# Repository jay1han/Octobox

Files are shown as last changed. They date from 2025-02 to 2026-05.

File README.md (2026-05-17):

# Octobox

Box for OrangePi Zero 2W running Fluidd/Moonraker/Klipper

# Hardware

## Components

### Actuator TB6612

Controls the actuator that opens/closes door.

[Instructables](https://www.instructables.com/Driving-Small-Motors-With-the-TB6612FNG/)

### Temperature sensor MLX90614

Reads the bed temperature via I2C.

[Instructables](https://www.instructables.com/MLX90614-Non-Contact-Infrared-Temperature-Sensor-W/)

### Relays

4-channel 5V module from [AliExpress](https://fr.aliexpress.com/item/1005007538301230.html).
Usage:
[Instructables](https://www.instructables.com/5V-4-Channel-Relay-Module-With-Arduino/)

- Box fan (12V): 120mm fan at the rear of the cabinet
- Bed cooler (12V): 80mm fan cools the bed after a print
- Printer power (220V)

### 2N7000 Transistor

Pack from [AliExpress](https://fr.aliexpress.com/item/1005006203763174.html).
Usage:
[2N7000 as switch](https://electronzap.com/brief-n-channel-enhancement-mode-mosfet-switch-circuit-2n7000-transistor/)

- Camera light (5V)
- CPU fan (5V): small 40mm fan cooling the CPU

## OrangePi Zero 2W pinout

| Number | GPIO | Alt | Value | | Number | GPIO | Alt | Value |
|---|---|---|---|---|---|---|---|---|
| | 3.3V | | I2C VCC | | | 5V | | |
| 264 | PI8  | SDA.1 | I2C SDA | | | 5V | | Power 5V |
| 263 | PI7  | SCL.1 | I2C SCL | | | GND  | | Power GND  |
| 269 | PI13 | PWM3 TXD.4  | | | 224 | PH0  | TXD.0 | |
| | GND  | | I2C GND | | 225 | PH1  | RXD.0 | |
| 226 | PH2  | TXD.5 | | | 257 | PI01 | | |
| 227 | PH3  | RXD.5 | | | | GND  | | |
| 261 | PI5  | SCL.0 TXD.2 | | | 270 | PI14 | PWM4 RXD.4  | Pusher PWM |
| | 3.3V | | Pusher VCC | | 228 | PH04 | | |
| 231 | PH7  | MOSI.1 | | | | GND  | | Pusher GND |
| 232 | PH8  | MISO.1 | | | 262 | PI6  | SDA.0 RXD.2 | Pusher 2 |
| 230 | PH6  | SCLK.1 | | | 229 | PH5  | CE.0 | Pusher 1 |
| | GND  | | | | 233 | PH9  | CE.1 | |
| 266 | PI10 | SDA.2 RXD.3 | | | 265 | PI9  | SCL.2 TXD.2 | Light |
| 256 | PI00 | Flash | | | | GND  | | MOSFET GND |
| 271 | PI15 | | | | 267 | PI11 | PWM1 | Fan40 |
| 268 | PI12 | PWM2 | | | | GND  | | Relay GND  |
| 258 | PI02 | | | | 76 | PC12 | | Fan120 |
| 272 | PI16 | | | | 260 | PI04 | | Printer |
| | GND  | | | | 259 | PI03 | | Fan80 |
	
# Software 

The software is a daemon started from systemd.
It listens on port `8080` and provides a basic HTTP server,
with a simple HTML page showing its current state.
The page contains minimal Javascript to update itself when needed.

The daemon also listens on port `8088` to serve [Moonraker's commands](#moonraker-interface).

## States

| State | When | Look for | Change to | Also do |
|---|---|---|---|---|
| (Initial) | booting | | OFF | retract Pusher, switch everything OFF |
| OFF | printer is off | event `power` | ON | switch Relay ON |
| ON | printer is powering on | Moonraker is ready | IDLE | |
| IDLE | ready for print | event `power` | OFF | switch everything OFF |
| | | Moonraker is printing | PRINTING  | switch Fan ON, Flash ON |
| PRINTING  | print job running | Moonraker is stopped  | COOLING | switch off Printer, start Cooler, extend Pusher |
| | | event `cancel` | PRINTING  | cancel job |
| COOLING | print job ended | bed temp < 35C | OFF | retract Pusher, switch everything OFF |
| | | event `power` | OFF | retract Pusher, switch everything OFF |
| (Any) | | event `reboot` | N/A | switch everything OFF then reboot |

## Moonraker API

Moonraker's
[HTTP API](https://moonraker.readthedocs.io/en/latest/external_api/introduction/#http-api-overview)
are used to update the daemon's internal state.

## Moonraker interface

The daemon provides an endpoint for Moonraker's
[HTTP devices](https://moonraker.readthedocs.io/en/latest/configuration/#generic-http-devices)
interface.

Moonraker must be configured

# Documents

- `Orange.pptx` shows the cabling of the Opi Zero 2W.
- `.FCStd` files for 3D models.
    - `CapL` : the filament guide at the top of the Z pole
    - `Fan8` : casing for the cooling fan
    - `KPS-CameraHD 2w` : the camera bracket
    - `Octobox 2W simple` : frame for the Opi and the board
    - `Wirecover` : to isolate the terminals of the power supply
    - `Touch` : housing for the touch sensor (ambient light)
    - `horiz2` : horizontal feeder for filament spool

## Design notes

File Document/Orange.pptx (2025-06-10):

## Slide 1

actual

Relay

1K

1K

1K

CPU

Cooler

10K

10K

Box

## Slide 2

enhanced

USB GND

1K

10K

1K

CPU Fan

1K

Relay

1K

Fan80

10K

10K

Fan120

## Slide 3

For USB

USB GND

1K

10K

1K

100

CPU Fan

1K

Relay

1K

Fan80

10K

10K

Fan120

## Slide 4

5V
GND
Fan80
Fan120
Relay
CPU Fan
Flash

5V:
- Flash
- Relay
- Pusher (?)
- CPU fan
- (Light)
12V:
- Fan120
- Fan80
64x44 M2
Direct:
- I2C(4)
- Touch in(3)

Flash

2K

PWM
A2
A1
En/

CPU Fan

Relay

2K

Fan120

Fan80

GND
3V3

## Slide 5

5V
GND
Fan80
Fan120
Relay
CPU Fan
Flash

5V:
- Flash
- Relay
- CPU fan
12V:
- Fan120
- Fan80
64x44 M2
Gate pull-down 10K
Flyback 1N4001 (50V)
Solid power 24AWG
Striped single 26AWG
Dotted signal 30AWG

10K

10K

Flash

CPU Fan

Relay

Fan120

Fan80

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
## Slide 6

5V:
- Flash
- Relay
- CPU fan
12V:
- Fan120
- Fan80
64x44 M2
Gate pull-down 47K
Flyback 1N4001 (50V)
Solid power 24AWG
Striped single 26AWG
Dotted signal 30AWG

10K

10K

Fan120

Fan80

10K

Flash

CPU Fan

Relay

10K

10K

PWM
A2
A1
En/

3V3

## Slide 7

5V:
- Flash
- Relay
- CPU fan
12V:
- Fan120
- Fan80
64x44 M2
Gate pull-down 47K
Flyback 1N4001 (50V)
Solid power 24AWG
Striped single 26AWG
Dotted signal 30AWG

10K

10K

Fan120

Fan80

10K

PWM
A2
A1
En/

3V3

Flash

CPU Fan

Relay

10K

10K

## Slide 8

5V:
- Flash
- Relay
- Pusher (?)
- (Light)
12V:
- Fan120
- Fan80
64x44 M2
Direct:
- I2C(4)
- Touch in(3)

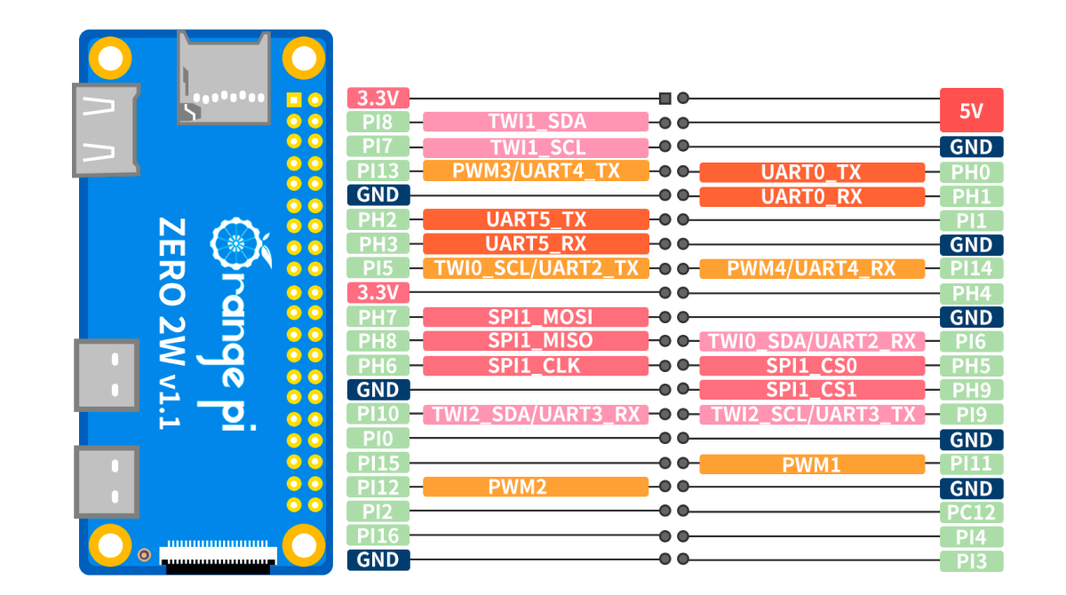
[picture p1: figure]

Pusher VCC

PWR 5V
PWR GND

I2C SCL
I2C VCC

I2C GND
I2C SDA
Pusher EN/
Pusher 1
Pusher 2

Pusher PWM
Flash
Relay
Fan80

CPU Fan
Fan120

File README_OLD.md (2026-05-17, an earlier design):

# Octobox OLD

Box for OrangePi Zero 2W running Octoprint for KP3S

## Server

You need to obtain an API key from Octoprint and store it in `api.key` in plain text.

### States

Modified for remote temperature sensor.

| State | When | Look for | Change to | Also do |
|---|---|---|---|---|
| (Initial) | starting Octobox | | Off | retract Pusher, capture Camera, switch everything OFF |
| Off | printer is off | event `power` | On | switch Relay ON, start Camera, start timeout |
| | | event `reboot` | N/A | reboot |
| | | event `refresh` | | capture image |
| On | printer is powering on | Octo is `Operational`  | Idle | |
| | | Octo has error | Off | switch everything OFF |
| | | Timeout elapsed | Off | switch everything OFF |
| | | event `refresh` | | capture image |
| Idle | ready for print | event `power` | Off | switch everything OFF |
| | | event `reboot` | N/A | reboot |
| | | Octo has error | Off | switch everything OFF |
| | | Octo is `Printing` | Printing  | |
| | | event `refresh` | | restart video |
| Printing  | print job running | Octo has error | Cooling | switch off Printer, start Cooler, extend Pusher |
| | | Octo is not `Printing` | Cooling | switch off Printer, start Cooler, extend Pusher |
| | | event `cancel` | Cooling | cancel Octo job, switch off Printer, start Cooler and Pusher |
| Cooling | print job ended | Octo has error | Off | retract Pusher, switch everything OFF |
| | | bed temp < 35C | Off | retract Pusher, switch everything OFF |
| | | event `power` | Off | retract Pusher, switch everything OFF |

## Peripherals

All methods take an optional argument to set the value,
or return the current value if no argument is given.
This module requires the module `python3-periphery`
and to be given access. See `install.sh`.

- `flash()` to switch the LED illuminating the camera.
This is used exclusively by the Camera module

- `fan()` to switch the cooling fan.

- `relay()` to switch the printer.

### Sensor

The MLX90614 allows monitoring ambient and bed temperatures at all times.
CPU sensor is now in this module.

### Camera

Upon initialization, kills current ustreamer if one is running.
When active, ustreamer is available at the URL
`http://localhost:8080`.

- `start()` starts ustreamer.

- `stop()` stops it. Calls `capture()`.

- `capture()` captures a still image into `/var/www/html/image.jpg`.

### Pusher

The motor is controlled by a TB6612FNG module.

## Display

This actually just updates the data files that are used by the HTML to display the page.

- `localIP` contains the local IP address.

- `state` contains the title of the document, which is the state returned by Octoprint.

- `temps` contains HTML snippet showing temperatures.

- `jobInfo` contains HTML snippet showing Job information (if any).

## Octoprint

This uses Octoprint's REST API to interact with it.
You need to obtain an API key from Octoprint and store it in `api.key` in plain text.

- Queries : `job` or `printer` queries.

- Requests : `connection` request to connect or disconnect the printer.

## Socket library

The file `/usr/share/octobox/socket` is used to pass events.
A user must first `lock()` it, then `read()` to or `write()` from it, 
then `free()` it.

## CGI

The GPI module uses the Socket library to send events to the running Octobox process.

- `power` to switch the printer.

- `reboot` to reboot Octobox.

- `cancel` cancels the print.

- `refresh` captures a new image.

## Documents

- `Orange.pptx` shows the cabling of the Opi Zero 2W.

- `.FCStd` files for 3D models.

    - `CapL` : the filament guide at the top of the Z pole
    
    - `Fan8` : casing for the cooling fan
    
    - `KPS-CameraHD 2w` : the camera bracket
    
    - `Octobox 2W simple` : frame for the Opi and the board
    
    - `Wirecover` : to isolate the terminals of the power supply
    
    - `Touch` : housing for the touch sensor (ambient light)

    - `horiz2` : horizontal feeder for filament spool
	
### OrangePi pinout

| Number | GPIO | Alt | Value | Color  |
|---|---|---|---|---|
| | 3.3V | | Pusher VCC | Orange |
| 264 | PI8  | SDA.1 | | |
| 263 | PI7  | SCL.1 | | |
| 269 | PI13 | PWM3 TXD.4  | Pusher PWM | Green  |
| | GND  | | Pusher GND | Black  |
| 226 | PH2  | TXD.5 | | |
| 227 | PH3  | RXD.5 | | |
| 261 | PI5  | SCL.0 TXD.2 | I2C SCL | Yellow |
| | 3.3V | | I2C VCC | Orange |
| 231 | PH7  | MOSI.1 | | |
| 232 | PH8  | MISO.1 | | |
| 230 | PH6  | SCLK.1 | | |
| | GND  | | | |
| 266 | PI10 | SDA.2 RXD.3 | | |
| 256 | PI00 | | Pusher EN  | Maroon |
| 271 | PI15 | | | |
| 268 | PI12 | PWM2 | CPU Fan | Green  |
| 258 | PI02 | | | |
| 272 | PI16 | | | |
| | GND  | | | |

| Number | GPIO | Alt | Value | |
|---|---|---|---|---|
| | 5V | | | |
| | 5V | | Power 5V  | Red |
| | GND  | | Power GND | Black  |
| 224 | PH0  | TXD.0 | | |
| 225 | PH1  | RXD.0 | | |
| 257 | PI01 | | | |
| | GND  | | | |
| 270 | PI14 | PWM4 RXD.4  | | |
| 228 | PH04 | | | |
| | GND  | | I2C GND | Violet |
| 262 | PI6  | SDA.0 RXD.2 | I2C SDA | Cream  |
| 229 | PH5  | CE.0 | | |
| 233 | PH9  | CE.1 | Pusher 1  | Blue |
| 265 | PI9  | SCL.2 TXD.2 | Pusher 2  | Violet |
| | GND  | | | |
| 267 | PI11 | PWM1 | Flash | Grey |
| | GND  | | | |
| 76 | PC12 | | Relay | Cream  |
| 260 | PI04 | | Fan120 | Blue |
| 259 | PI03 | | Fan80 | Violet |

## TODO

### Hardware

- Actuator

- Temperature sensor(s): MLX90614

	- Turn off printer at job's end and turn on cooling fan
	
	- Use sensor to monitor bed temperature and turn off cooling fan
	
- Recheck install script

- Better lighting for camera

### Software

HTTP GETtable file `http://octo2w.local/info` returns the following information
in INI format (`key=value`):

| Field | Type | Example |
|---|---|---|
| filename | string | `octobox-part` |
| completion  | float  | `15.6` |
| remaining | HH:MM  | `01:32` |

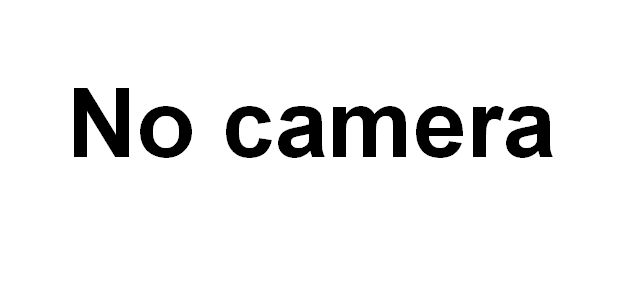
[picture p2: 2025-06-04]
Server/files/nocamera.jpg

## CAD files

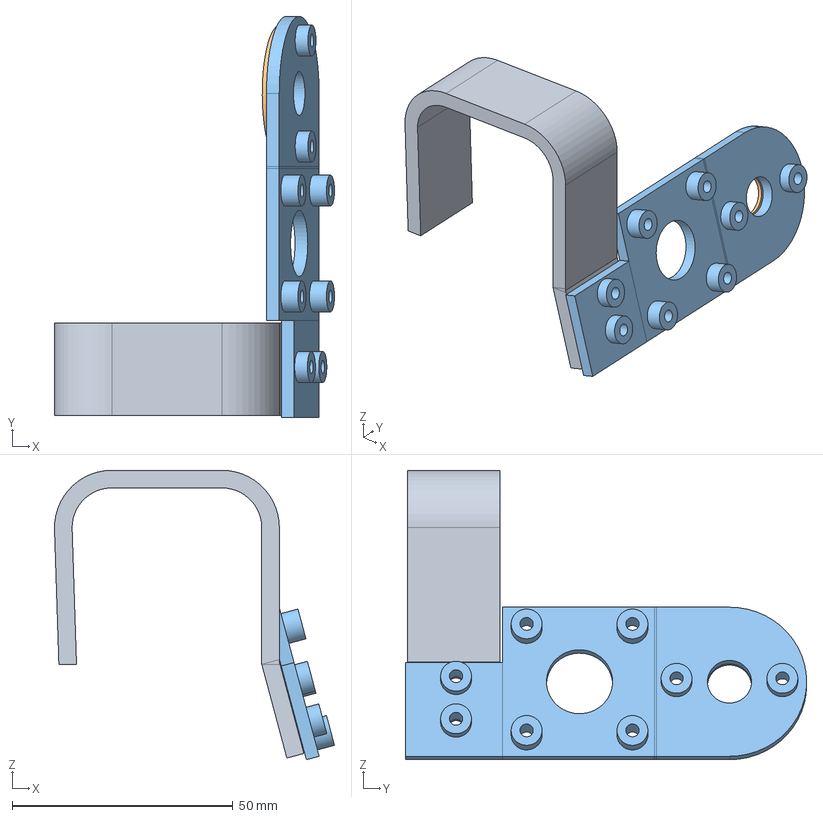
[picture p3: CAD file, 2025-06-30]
Design/KPS-CameraHD bigled.FCStd
63.5 x 91.0 x 65.6 mm
Clip
Bigled
Camholes

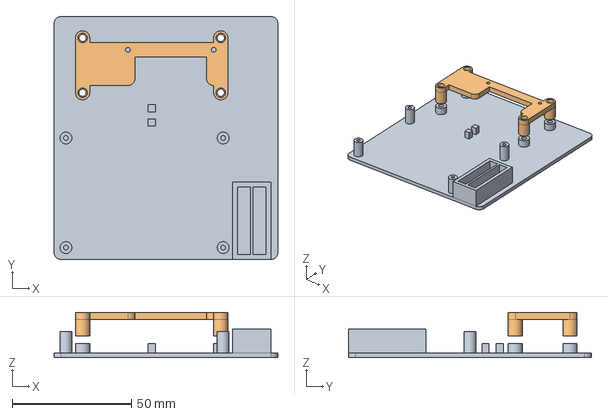
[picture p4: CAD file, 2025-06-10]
Document/Octobox 2W relays.FCStd
94.0 x 102.0 x 19.0 mm
Base
Fan

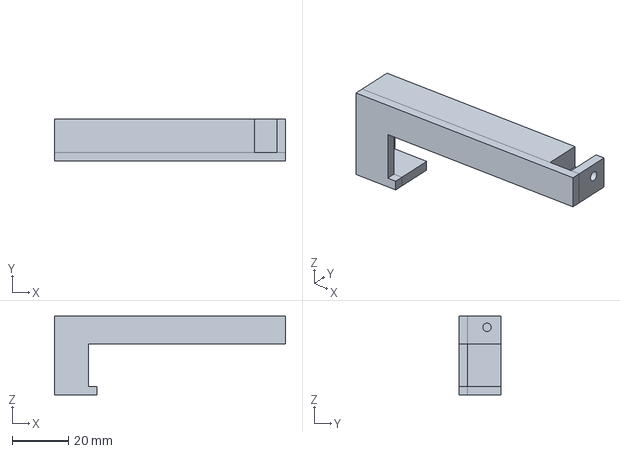
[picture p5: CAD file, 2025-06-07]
Design/Wirecover.FCStd
82.0 x 15.0 x 28.0 mm

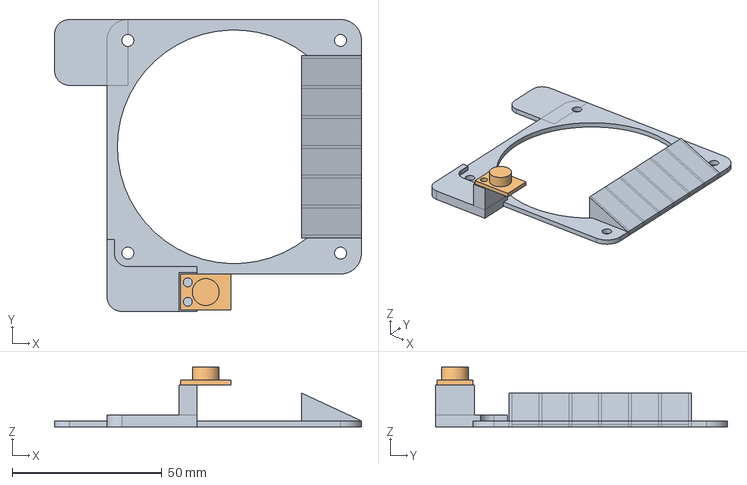
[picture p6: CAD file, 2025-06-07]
Document/Fan8-slant.FCStd
102.5 x 97.5 x 20.0 mm
Vent
Sensor

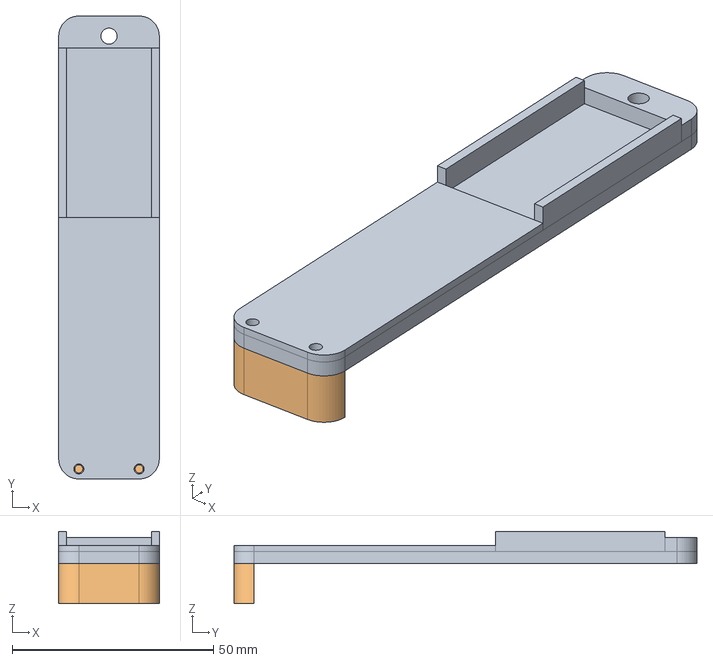
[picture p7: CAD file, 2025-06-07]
Design/Pusher.FCStd
25.0 x 115.0 x 18.0 mm
Tab

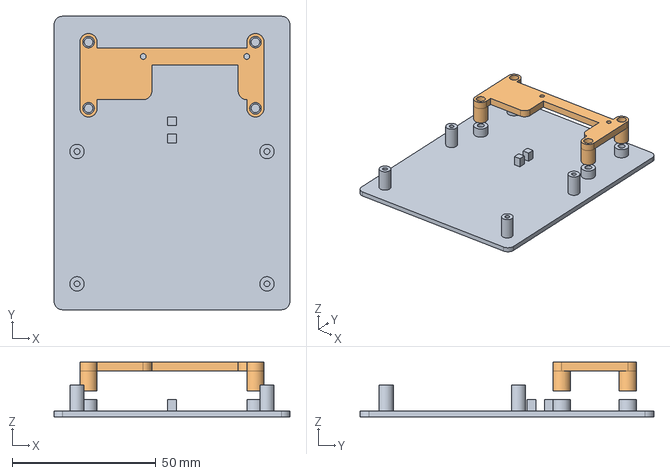
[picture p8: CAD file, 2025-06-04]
Document/Octobox 2W double.FCStd
82.0 x 102.0 x 19.0 mm
Base
Fan

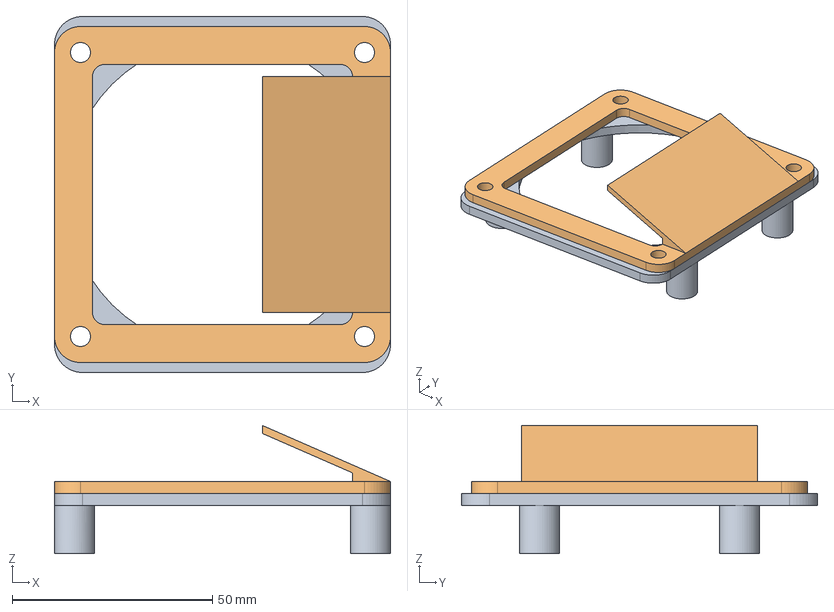
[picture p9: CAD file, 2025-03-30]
Design/Fan8.FCStd
84.0 x 89.0 x 32.0 mm
Vent

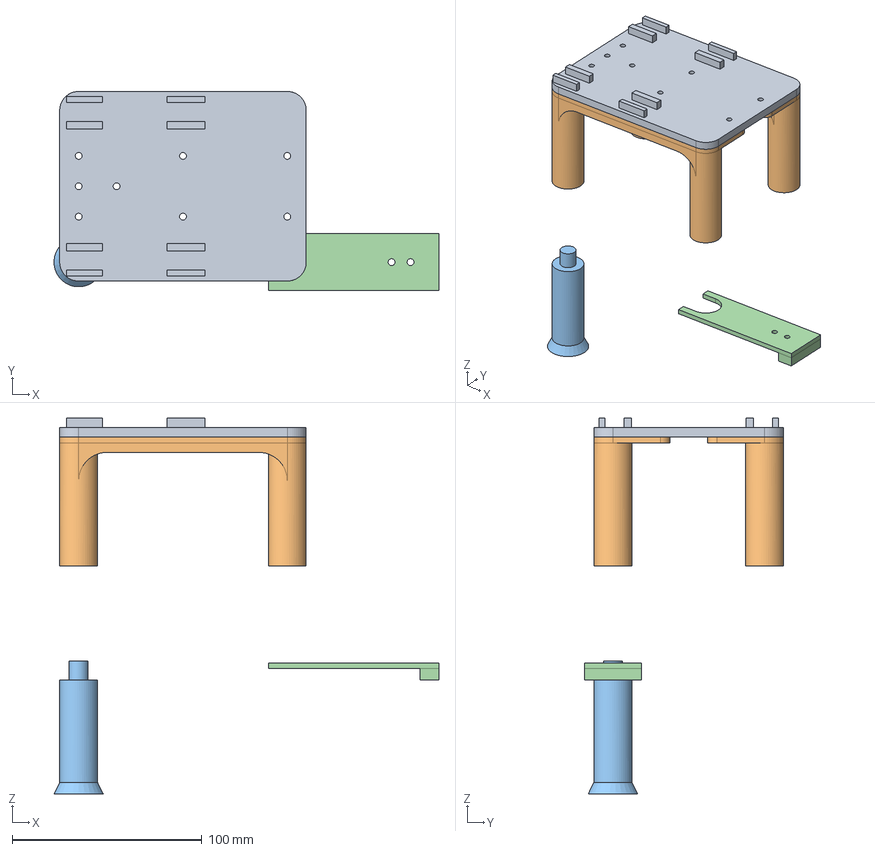
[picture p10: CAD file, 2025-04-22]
Document/Support_long.FCStd
203.0 x 105.0 x 198.0 mm
Top
Mid1 x 2
Leg1
Pusher

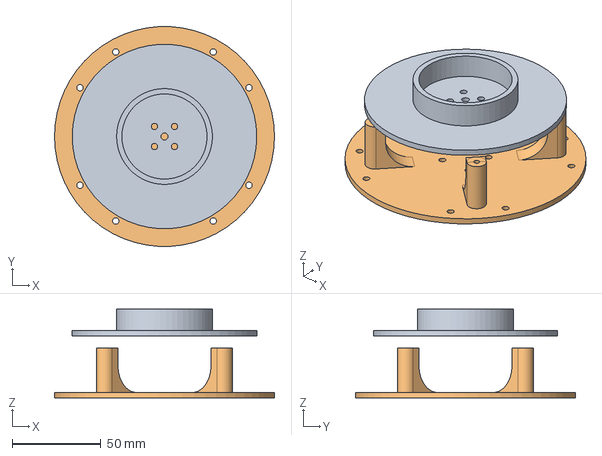
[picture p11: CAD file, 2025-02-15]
Design/horiz2.FCStd
124.0 x 123.8 x 50.0 mm
Wheel
Mid

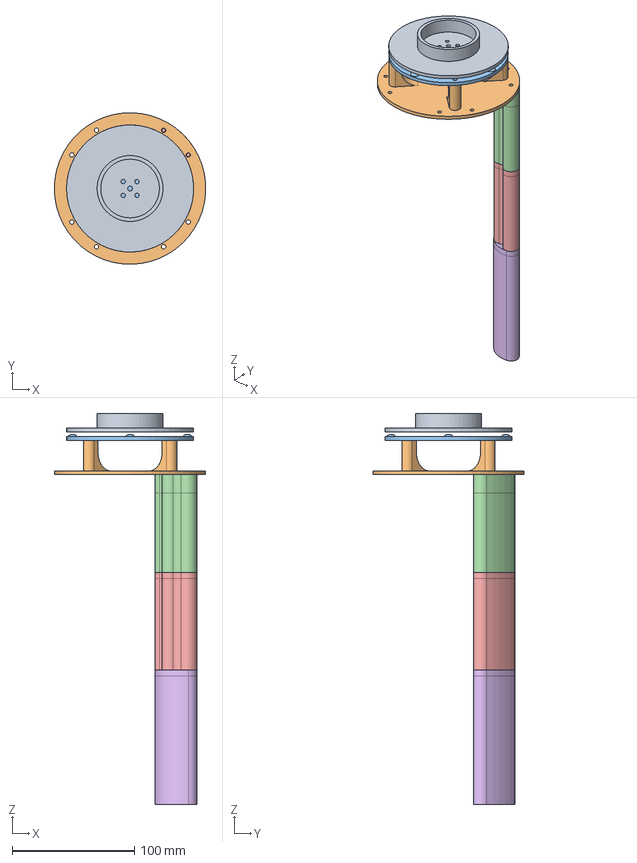
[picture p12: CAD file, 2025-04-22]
Document/horiz2.FCStd
123.9 x 123.9 x 320.0 mm
Wheel
Mid
Top
Leg1
Foot1
Shoe1

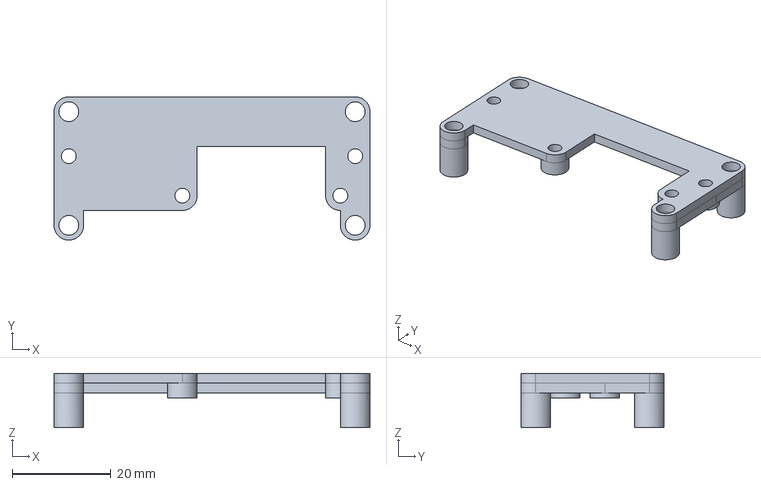
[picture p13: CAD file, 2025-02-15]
Design/Octobox 2W simple.FCStd
64.0 x 29.0 x 11.0 mm

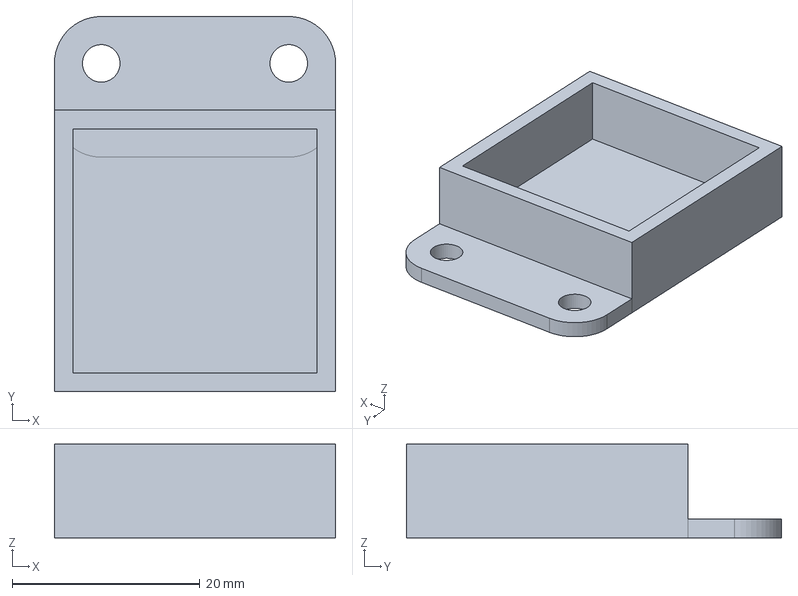
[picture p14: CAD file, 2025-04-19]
Document/Touch.FCStd
30.0 x 40.0 x 10.0 mm

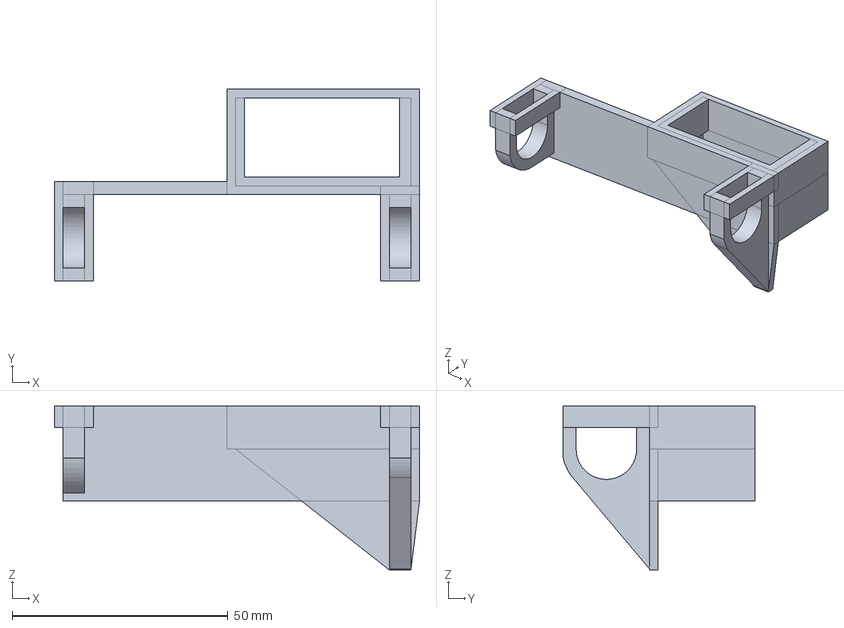
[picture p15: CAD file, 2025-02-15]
Design/CapL.FCStd
84.6 x 44.4 x 38.0 mm

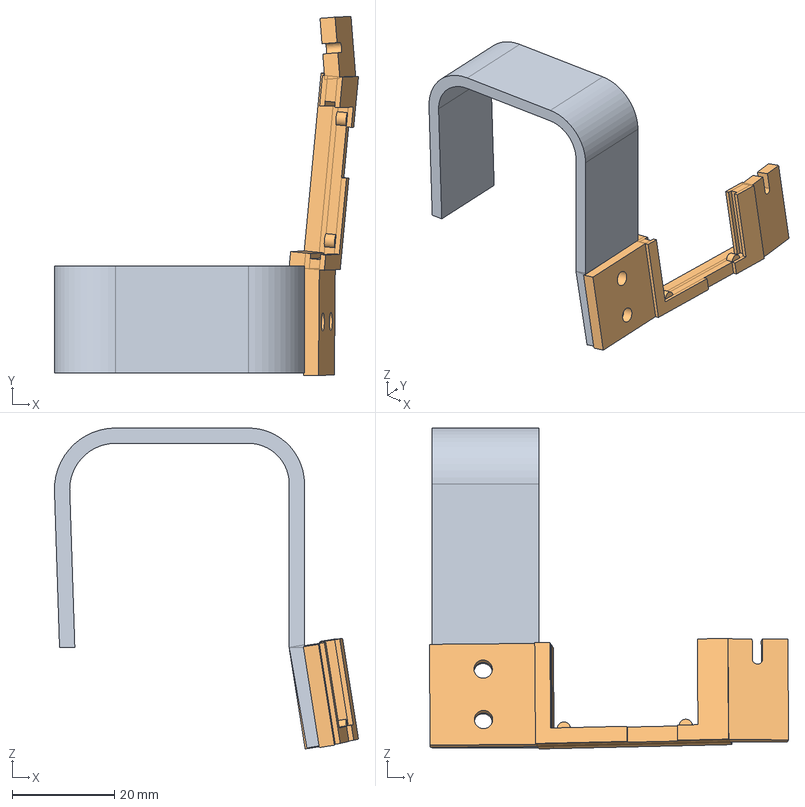
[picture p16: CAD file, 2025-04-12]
Document/KPS-CameraHD 2w.FCStd
59.6 x 70.4 x 62.9 mm
Clip
Frame

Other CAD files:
Design/CapGuide.FCStd
Document/Fan8.FCStd
Design/horiz.FCStd
Document/Octobox 2W simple.FCStd
Design/Cap.FCStd
Design/Cap_straight_slot.FCStd
Design/KPS-CameraHD 2w.FCStd
Design/Support_long.FCStd
Design/Touch.FCStd

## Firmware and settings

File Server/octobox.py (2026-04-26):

#!/usr/bin/python3

from time import sleep
from datetime import datetime, timedelta
from enum import Enum
import sys, subprocess

from octo_periph import Peripheral, Camera
from octo_disp import Display
from octo_print import Octoprint
from octo_socket import Socket

tempCold = 35.0

class State(Enum):
    Off      = 0
    On       = 1
    Idle     = 2
    Printing = 3
    Cooling  = 4

class Octobox:
    def __init__(self):
        self.state = State.Off
        self.octo_state = ''
        self.timeout = None
        self.elapsed = 0

        self.p = Peripheral()
        self.c = Camera(self.p)
        self.o = Octoprint()
        self.d = Display()
        self.s = Socket()

        self.d.setState('Printer Off')

    def __del__(self):
        pass

    def setTimeout(self, seconds):
        if seconds == 0:
            self.timeout = None
        else:
            self.timeout = datetime.now() + timedelta(seconds = seconds)

    def isTimedout(self):
        if self.timeout is not None and datetime.now() > self.timeout:
            self.timeout = None
            print('Timeout', file=sys.stderr)
            return True
        else:
            return False

    def powerOff(self):
        print('Power Off', file=sys.stderr)
        self.c.stop()
        self.p.fan(False)
        self.p.cooler(False)
        self.p.pusher(False)
        self.p.power(False)
        self.p.cpu(False)

    def powerOn(self):
        print('Power On', file=sys.stderr)
        self.d.clearInfo()
        self.p.power(True)
        self.p.fan(True)
        self.p.cpu(True)

    def reboot(self):
        print('Reboot', file=sys.stderr)
        self.powerOff()
        self.p.stop()
        ps = subprocess.run(['/usr/sbin/systemctl', 'reboot'])
        sys.exit(0)
    
    def loop(self):
        octo_state = self.o.getState()
        event = self.s.read()
        tempExt, tempBed = self.o.getTemp()
        tempCpu, tempOut, tempAmb = self.p.temps()

        if event != '' or self.octo_state != octo_state:
            print(f'State {self.state}: State "{octo_state}", Event "{event}"', file=sys.stderr)
            self.octo_state = octo_state

        if self.state == State.Off:
            if octo_state.startswith('Operational'):
                self.setTimeout(0)
                self.state = State.Idle
            elif event == 'refresh':
                self.c.capture()
            elif event == 'power':
                self.powerOn()
                self.c.start()
                sleep(1)
                self.o.connect()
                self.setTimeout(15)
                self.state = State.On
            elif event == 'reboot':
                self.reboot()

        elif self.state == State.On:
            if event == 'refresh':
                self.c.capture()
            elif octo_state.startswith('Operational'):
                self.setTimeout(0)
                self.state = State.Idle
            elif octo_state.startswith('Error') or octo_state.startswith('Offline'):
                print('Error', file=sys.stderr)
                self.o.disconnect()
                self.powerOff()
                self.state = State.Off
            elif self.isTimedout():
                self.o.disconnect()
                self.powerOff()
                self.state = State.Off

        elif self.state == State.Idle:
            if octo_state.startswith('Printing'):
                print('Print start', file=sys.stderr)
                self.state = State.Printing
                self.d.start()
            elif octo_state.startswith('Error') or octo_state.startswith('Offline'):
                print('Error', file=sys.stderr)
                self.o.disconnect()
                self.powerOff()
                self.state = State.Off
            elif event == 'refresh':
                self.c.refresh()
            elif event == 'power':
                print('Power Off', file=sys.stderr)
                self.o.disconnect()
                self.powerOff()
                self.state = State.Off
            elif event == 'reboot':
                self.reboot()

        elif self.state == State.Printing:
            if not octo_state.startswith('Printing'):
                self.state = State.Cooling
            elif event == 'refresh':
                self.c.refresh()
            elif event == 'cancel':
                self.o.cancel()
                self.state = State.Cooling
                
            if self.state == State.Cooling:
                print('Print ended', file=sys.stderr)
                self.d.end()
                self.p.cooler(True)
                self.p.pusher(True)

        elif self.state == State.Cooling:
            if octo_state.startswith('Error'):
                print('Error', file=sys.stderr)
            if tempOut < tempCold or tempOut < (tempAmb + 3.0):
                print('Cold', file=sys.stderr)
                self.state = State.Off
            elif event == 'power':
                print('Power Off', file=sys.stderr)
                self.state = State.Off
            elif event == 'refresh':
                self.c.refresh()
                
            if self.state == State.Off:
                self.o.disconnect()
                self.powerOff()
                
        self.d.setTemps(tempAmb, tempExt, tempBed, tempOut, tempCpu,
                        tempCold if self.state == State.Cooling else 0.0)
        
        if self.state == State.Off:
            self.d.setState('Printer Off')
        elif self.state == State.Idle:
            self.d.setState(octo_state)
            jobInfo = self.o.getJobInfo()
            self.d.setJobInfo(jobInfo)
        elif self.state == State.Printing:
            self.d.setState(octo_state)
            jobInfo = self.o.getJobInfo()
            self.elapsed = jobInfo.currentTime
            self.d.setJobInfo(jobInfo)
        elif self.state == State.Cooling:
            self.d.setState('Cooling')
            self.d.setElapsed(self.elapsed)

    sleep(0.1)
            
octobox = Octobox()

while True:
    octobox.loop()
    sleep(1)

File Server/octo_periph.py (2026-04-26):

import subprocess, os, re, sys, shutil, threading, signal
from time import sleep
from datetime import datetime, timedelta
from periphery import GPIO, I2C, PWM

_GPIO_FLASH  = 76
_GPIO_COOLER = 259
_GPIO_POWER  = 260
_GPIO_CPU    = 258
_GPIO_FAN    = 272
_GPIO_PUSHER = 229     # low active
_GPIO_A1     = 233
_GPIO_A2     = 265

_PWM_PUSHER  = 1

_I2C_TEMP    = "/dev/i2c-0"
_TEMP_ADDR   = 0x5A
_REG_TOBJ1   = 0x07
_REG_TA      = 0x06

RESOLUTION   = '1280x800'
WWW          = '/var/www/html'
    
class Peripheral:
    def __init__(self):
        self._flashGpio = GPIO("/dev/gpiochip0", _GPIO_FLASH, "out")
        self._flashGpio.write(False)
        self._coolerGpio = GPIO("/dev/gpiochip0", _GPIO_COOLER, "out")
        self._coolerGpio.write(False)
        self._fanGpio = GPIO("/dev/gpiochip0", _GPIO_FAN, "out")
        self._fanGpio.write(False)
        self._powerGpio = GPIO("/dev/gpiochip0", _GPIO_POWER, "out")
        self._powerGpio.write(False)
        self._cpuGpio = GPIO("/dev/gpiochip0", _GPIO_CPU, "out")
        self._cpuGpio.write(False)
        
        self._pusherEn = GPIO("/dev/gpiochip0", _GPIO_PUSHER, "out")
        self._pusherEn.write(False)
        self._pusher1 = GPIO("/dev/gpiochip0", _GPIO_A1, "out")
        self._pusher1.write(False)
        self._pusher2 = GPIO("/dev/gpiochip0", _GPIO_A2, "out")
        self._pusher2.write(False)
        self._pusherPWM = PWM(0, _PWM_PUSHER)
        self._pusherPWM.frequency = 1000
        self._pusherPWM.duty_cycle = 0.5
        self._pushed = True
        self._thread = None
        self._pushEvent = threading.Event()
        self.pusher(False)

        self._tempI2C = I2C(_I2C_TEMP)
        
        self._tAmbient = 0.0
        
    def flash(self, state: bool):
        self._flashGpio.write(state)
    
    def fan(self, state: bool):
        self._fanGpio.write(state)

    def power(self, state:bool):
        self._powerGpio.write(state)

    def cooler(self, state: bool):
        self._coolerGpio.write(state)

    def cpu(self, state: bool):
        self._cpuGpio.write(state)

    def pushing(self, state: bool):
        print(f'Pusher({state}) started', file=sys.stderr)
        timeout = datetime.now() + timedelta(seconds = 30)
        self._pushed = state
        self._pusherPWM.enable()
        self._pusherEn.write(False)
        self._pusher1.write(state)
        self._pusher2.write(not state)
        self._pusherEn.write(True)
        while datetime.now() < timeout and not self._pushEvent.is_set():
            sleep(0.5)
        self._pusherEn.write(False)
        self._pusherPWM.disable()
        self._pusher1.write(False)
        self._pusher2.write(False)
        self._thread = None
        print(f'Pusher({state}) done', file=sys.stderr)

    def pusher(self, state: bool, wait: bool = False):
        if self._pushed != state:
            if self._thread is not None and self._thread.is_alive():
                self._pushEvent.set()
                self._thread.join(1.0)
                self._pushEvent.clear()

            if wait:
                self.pushing(state)
            else:
                print('Push async', file=sys.stderr)
                self._thread = threading.Thread(target=self.pushing, args=[state], daemon=True)
                self._thread.start()

    def temps(self) -> (float, float, float):
        with open('/sys/class/thermal/thermal_zone0/temp', 'r') as temp:
            tCpu = int(temp.read().strip()) / 1000.0

        tObject = 0.0
        tAmbient = 0.0
        dummy = bytearray(3)
        
        msgs = [I2C.Message([_REG_TOBJ1]), I2C.Message(dummy, True)]
        try:
            msg = self._tempI2C.transfer(_TEMP_ADDR, msgs)
        except Exception as e:
            print(e, file=sys.stderr)
        resp = msgs[1].data
        data = resp[0] | (resp[1] << 8)
        tObject = float(data) * 0.02 - 273.15

        msgs = [I2C.Message([_REG_TA]), I2C.Message(dummy, True)]
        try:
            msg = self._tempI2C.transfer(_TEMP_ADDR, msgs)
        except Exception as e:
            print(e, file=sys.stderr)
        resp = msgs[1].data
        data = resp[0] | (resp[1] << 8)
        tAmbient = float(data) * 0.02 - 273.15
        
        self._tAmbient = tAmbient
        
        return tCpu, tObject, tAmbient

    def stop(self):
        self._flashGpio.write(False)
        self._flashGpio.close()
        self._coolerGpio.write(False)
        self._coolerGpio.close()
        self._fanGpio.write(False)
        self._fanGpio.close()
        self._powerGpio.write(False)
        self._powerGpio.close()
        self._cpuGpio.write(False)
        self._cpuGpio.close()
        
        self.pusher(False, wait=True)
        self._pusherEn.close()
        self._pusher1.close()
        self._pusher2.close()
        self._pusherPWM.close()

        if self._tempI2C is not None:
            self._tempI2C.close()

    def __del__(self):
        self.stop()
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

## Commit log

2025-04-12 Better fan
    [Fan8.FCStd, KPS-CameraHD 2w.FCStd]
2025-05-07 camera, at last
2025-06-01 prep MLX sensor
2025-06-04 doc & design
    [Octobox 2W double.FCStd, Wirecover.FCStd]
2025-06-08 frame dump
2025-06-27 cpu fan
2025-10-06 CPU fan always on
